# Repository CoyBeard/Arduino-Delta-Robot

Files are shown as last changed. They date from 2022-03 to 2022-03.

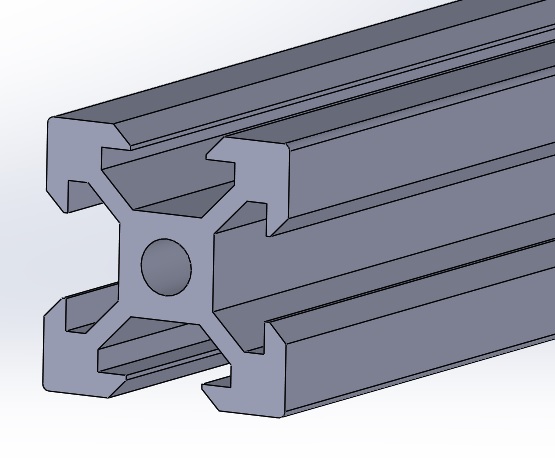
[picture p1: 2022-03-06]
2020-aluminium-profile-v-slot-solidwork2016-1.snapshot.8/2020 aluminium profile v slot.jpg

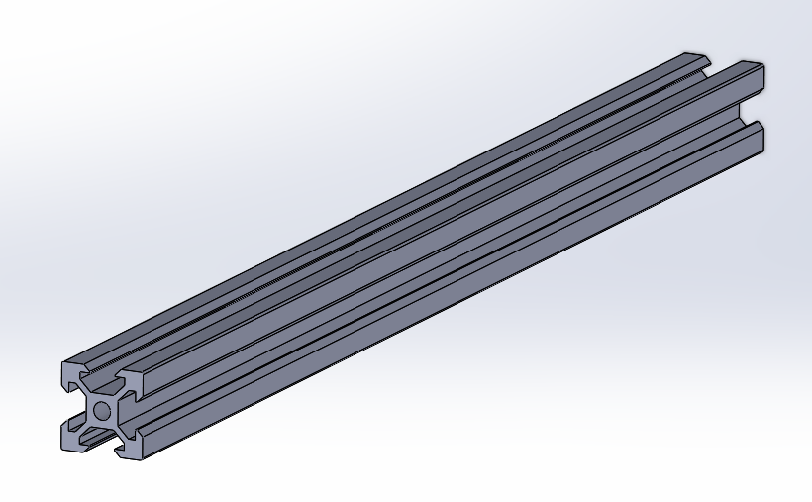
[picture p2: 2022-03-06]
2020-aluminium-profile-v-slot-solidwork2016-1.snapshot.8/2020 aluminium profile v slot solidwork 2016.png

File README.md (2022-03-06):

# Arduino-Delta-Robot
All CAD and code as seen in my YouTube video

All CAD was drawn in Autodesk Inventor But in the STEP Files the assembly is also saved as .stp

The code isn't as developed as I wanted it to be but the project had to be completed in a month

Feel free to incorporate some of these resorces into your own delta robot build!

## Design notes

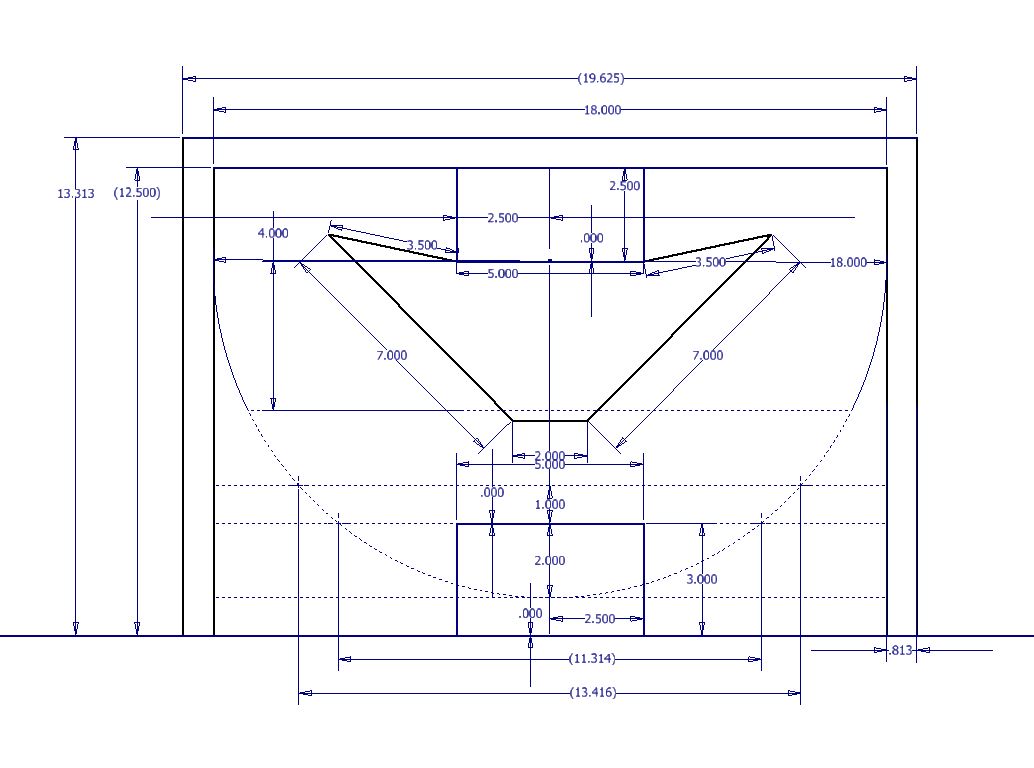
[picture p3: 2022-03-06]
Kenimatics Sketch.JPG

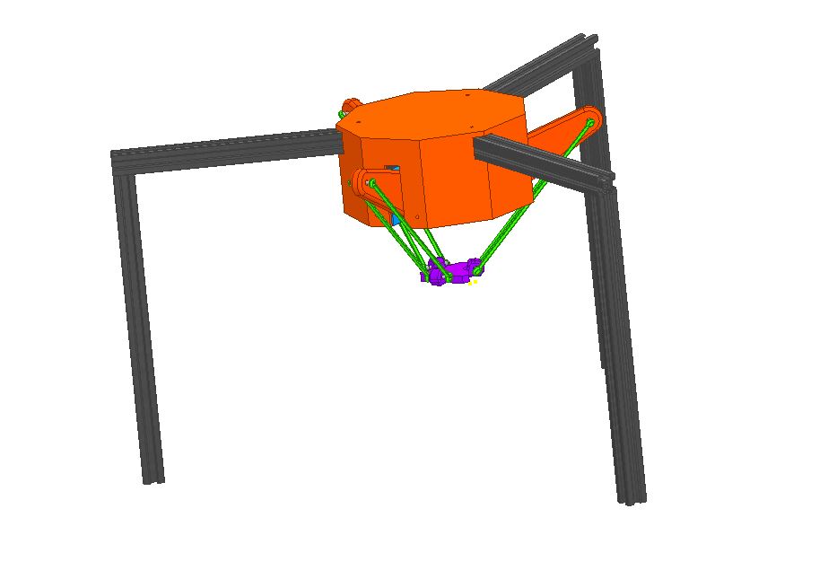
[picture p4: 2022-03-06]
Delta Robot V1 3D Model.JPG

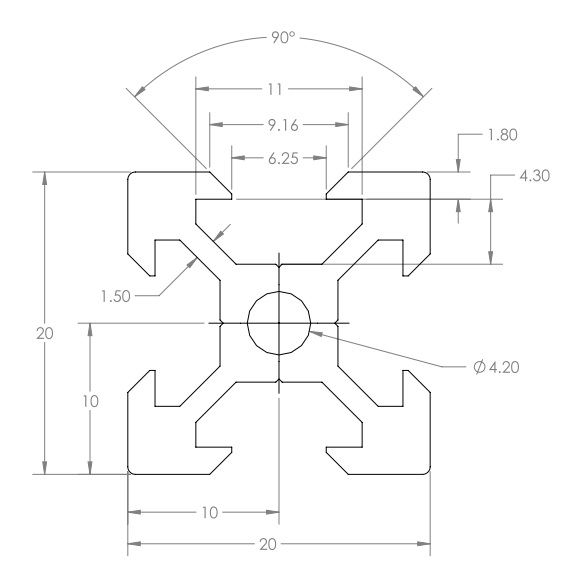
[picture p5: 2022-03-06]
2020-aluminium-profile-v-slot-solidwork2016-1.snapshot.8/5j.jpg

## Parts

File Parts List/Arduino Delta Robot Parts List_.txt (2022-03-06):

Arduino Delta Robot Parts List:
CNC 3D Printer Driver Kit, MYSWEETY 39PCS 3D Printer CNC Module Kit, 3D Printer CNC Controller Kit, Nema 17 Stepper Motor & Stepper Motor Driver with Heat Sink:

https://www.amazon.com/Printer-Driver-MYSWEETY-Controller-Stepper/dp/B08PYVPGNW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

BUD Industries JBH-4961-KO Steel NEMA 1 Sheet Metal Box 6" L x 10" W, Gray

https://www.amazon.com/gp/product/B005UPA10Y/ref=ppx_yo_dt_b_search_asin_title?ie=UTF8&psc=1

Zeelo GT2 Timing Belt Pulley, 8pcs 5mm 20 Teeth Timing Pulley Wheel and GT2 5 Meters Rubber 2mm Pitch 6mm Wide Timing Belt with Allen Wrench for 3D Printer CNC

https://www.amazon.com/gp/product/B07XG9JN5B/ref=ppx_yo_dt_b_search_asin_title?ie=UTF8&psc=1

3D Printer - Deek Robot 12Pcs/Set 3D Printer Accessories M3 Or M4 5347 Delta Buckle Ball Caps Paralleled Carbon Rod Joints - (Size: for M4)

https://www.amazon.com/gp/product/B07KX2CXX5/ref=ppx_yo_dt_b_search_asin_title?ie=UTF8&th=1

uxcell M4 x 170mm 304 Stainless Steel Fully Threaded Rod Bar Studs Fastener 10 Pcs

https://www.amazon.com/gp/product/B01MA5XUOI/ref=ppx_yo_dt_b_search_asin_title?ie=UTF8&psc=1

Iverntech 4pcs 700mm 2020 V Type Black European Standard Anodized Linear Rail Aluminum Profile Extrusion for DIY 3D Printer and CNC Machine

https://www.amazon.com/gp/product/B087PVDDX4/ref=ppx_yo_dt_b_search_asin_title?ie=UTF8&psc=1

uxcell 685ZZ Deep Groove Ball Bearings Z2 5mm X 11mm X 5mm Double Shielded Carbon Steel 12pcs

https://www.amazon.com/gp/product/B08198NQ7Y/ref=ppx_yo_dt_b_search_asin_title?ie=UTF8&psc=1

uxcell A15113000ux1262 5 Pcs 5mm x 100mm DIY RC Car Model Straight Metal Round Shaft Rod Bars (Pack of 5)

https://www.amazon.com/gp/product/B01B27MJC6/ref=ppx_yo_dt_b_search_asin_title?ie=UTF8&psc=1

VIGRUE M3 M4 M5 M6 Screw Bolt Nut Assortment Set, Button Head & Socket Head Metric Screws, 304 Stainless Steel, 588Pcs Silver

https://www.amazon.com/gp/product/B08MDXD1BN/ref=ppx_yo_dt_b_search_asin_title?ie=UTF8&psc=1

VIGRUE 184Pcs 2020 Series T Nuts, M3 M4 M5 T Slot Nut Hammer Head Fastener Nut Nickel Plated Carbon Steel with 4 Matching Wrenches for Aluminum Profile

https://www.amazon.com/gp/product/B07PLKVW69/ref=ppx_yo_dt_b_search_asin_title?ie=UTF8&psc=1

Toggle Switch Submini SPDT & DPDT On Off On Latching, Momentary, Short Shaft, Switch Assortment Kit, 31 pcs, 10 Types

https://www.amazon.com/gp/product/B08T5XS9Q3/ref=ppx_yo_dt_b_search_asin_title?ie=UTF8&psc=1
ALITOVE DC 12V 10A 120W Power Supply Adapter Transformer Switch AC 110V / 220V to DC 12V 10amp Switching Converter LED Driver for LED Strip Light CCTV Camera Security System

https://www.amazon.com/gp/product/B078RTV9C4/ref=ppx_yo_dt_b_search_asin_title?ie=UTF8&psc=1

Zixtec 10 Pack LM2596 DC-DC Buck Converter Step Down Module Power Supply DIP Output 1.25V-30V 3A (ZT001)

https://www.amazon.com/gp/product/B07VVXF7YX/ref=ppx_yo_dt_b_search_asin_title?ie=UTF8&psc=1

Liberty 22mm mounting Hole Latch Emergency Stop Button Switch red, with 60mm Emergency Stop Sign 1NO 1NC, 660V 10A (4PCS)

https://www.amazon.com/gp/product/B08ZCDHZ3R/ref=ppx_yo_dt_b_search_asin_title?ie=UTF8&psc=1

OVERTURE PLA Filament 1.75mm PLA 3D Printer Consumables, 1kg Cardboard Spool (2.2lbs), Dimensional Accuracy +/- 0.03mm, Fit Most FDM Printer (Black 1-Pack)

https://www.amazon.com/gp/product/B07PGY2JP1/ref=ppx_yo_dt_b_search_asin_title?ie=UTF8&psc=1

Eryone Silk PLA Filament 1.75mm, Silky Shiny 3D Printing Material for 3D Printer and 3D Pen, 1kg 1 Spool, 1.75mm, Silver

https://www.amazon.com/gp/product/B07KFX5THQ/ref=ppx_yo_dt_b_search_asin_title?ie=UTF8&psc=1

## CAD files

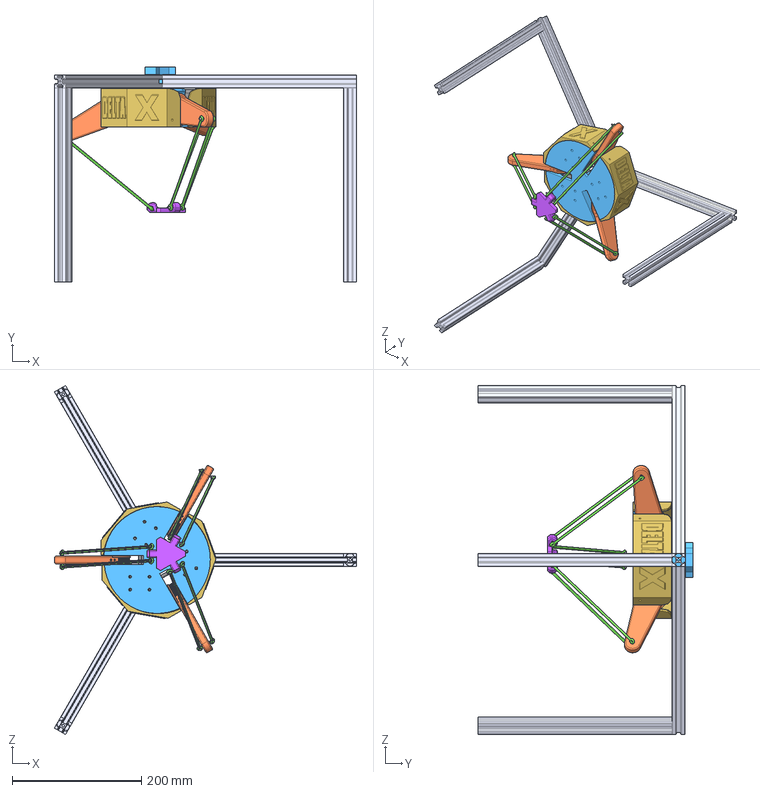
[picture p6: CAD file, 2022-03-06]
STEP Files/Delts Robot V1 Assembly.stp
467.4 x 332.5 x 539.6 mm
Delts Robot Motor Hub
Nema 17 CNC Kit Stepper Motor x 3
Delta Robot Arm Segment One x 3
Delta Robot Arm Segment Two x 6
Delts Robot Cairage
Delts Robot Arm Joint Rod x 6
2020 aluminium profile v slot solidwork2016 x 6
Small GT2 Belt Pully
Delta Robot Siding Piece x 3

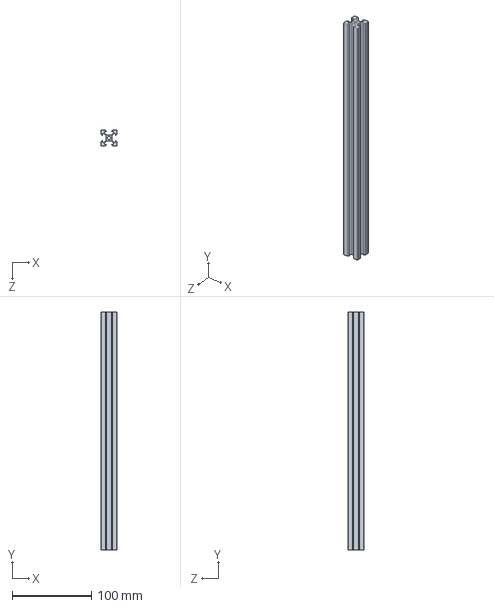
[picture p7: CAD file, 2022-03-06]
2020-aluminium-profile-v-slot-solidwork2016-1.snapshot.8/2020 aluminium profile v slot solidwork2016.SLDPRT
20.0 x 300.0 x 20.0 mm

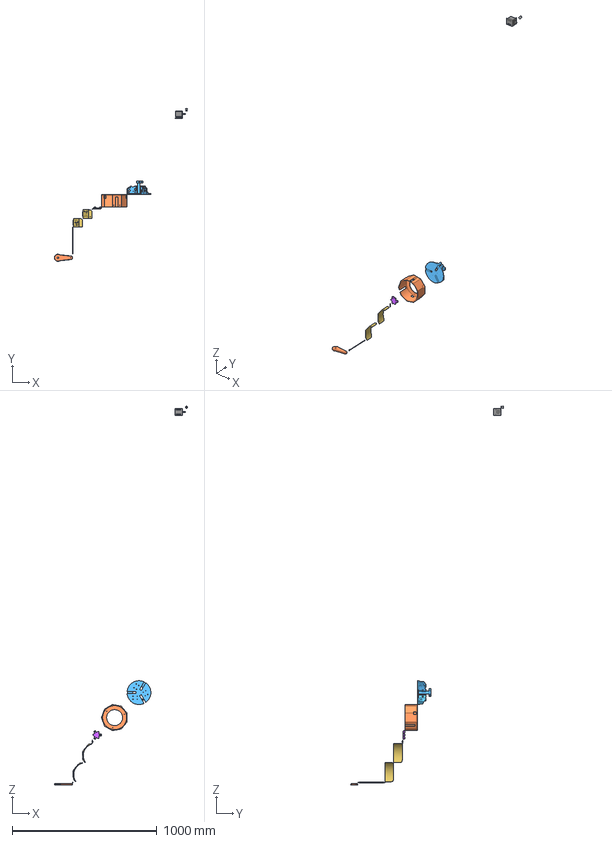
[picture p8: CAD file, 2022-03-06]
STEP Files/Other Parts.stp
921.9 x 1056.5 x 2621.0 mm
Delta Robot Arm Segment One
Delta Robot Arm Segment Two
Delta Robot Siding Piece KUKA
Delta Robot Siding Piece
Delts Robot Arm Joint Rod
Delts Robot Cairage
Delts Robot Casing
Delts Robot Motor Hub
Nema 17 CNC Kit Stepper Motor
Small GT2 Belt Pully

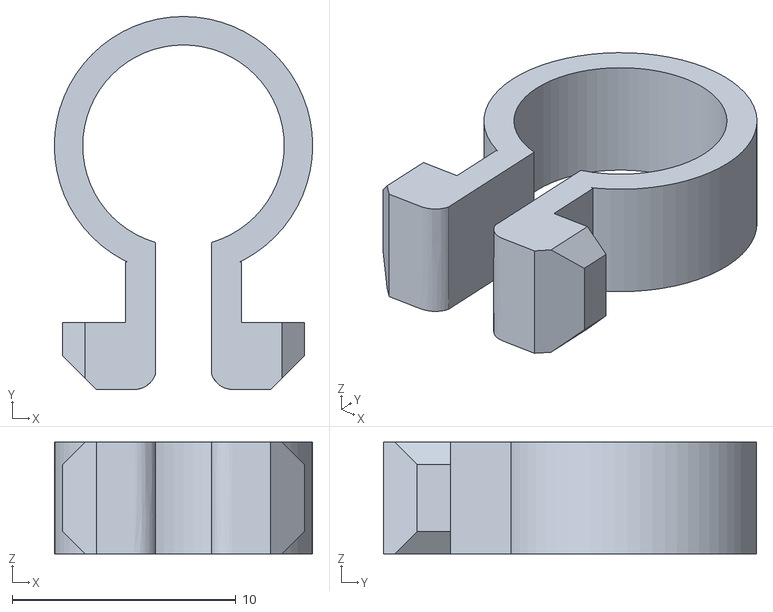
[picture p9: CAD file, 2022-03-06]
STLs V3/Cable_management_for_extrusion_2020/files/cable_2020_large (2021_05_27 07_37_48 UTC).stl
11.6 x 16.7 x 5.00

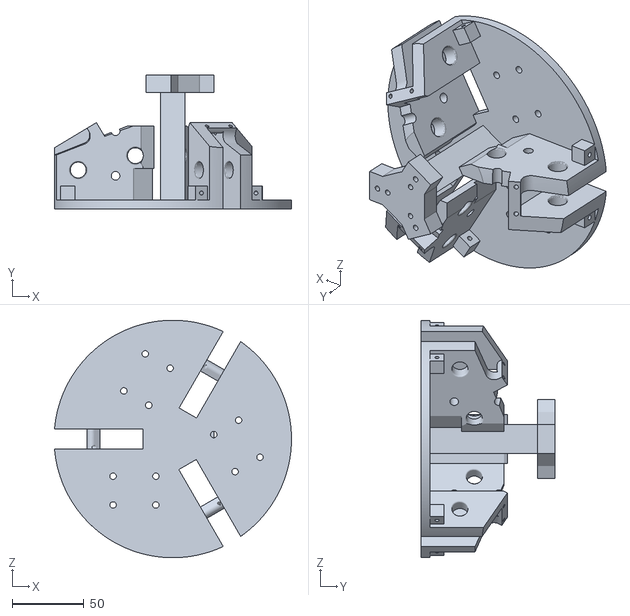
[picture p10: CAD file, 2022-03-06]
STLs V3/Delts Robot Motor Hub (2021_05_27 07_37_48 UTC).stl
164.8 x 93.0 x 165.1

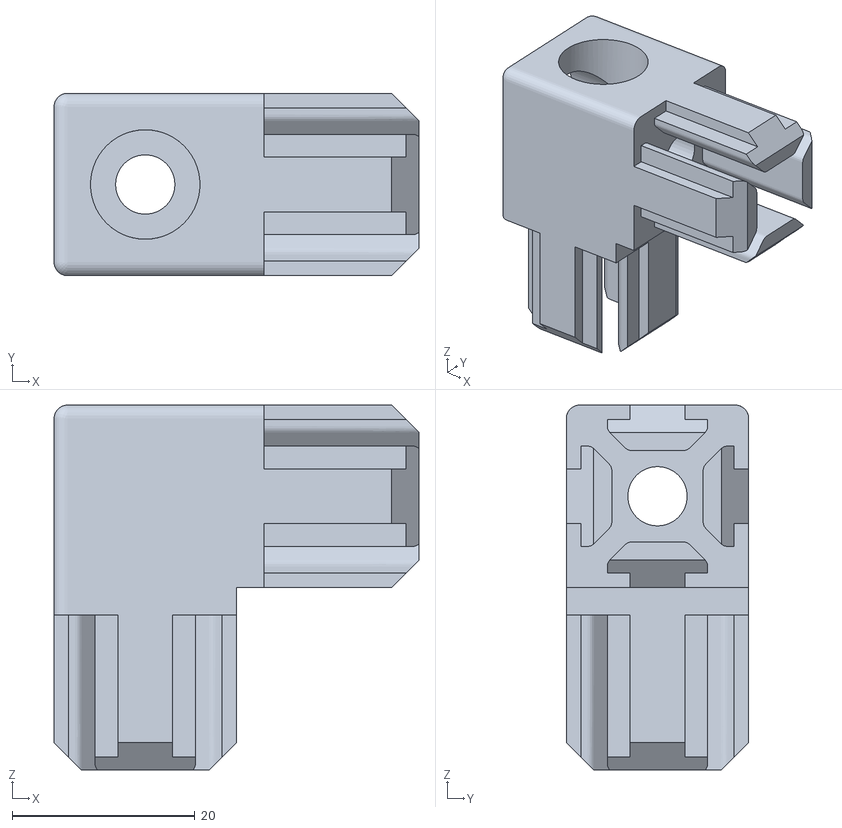
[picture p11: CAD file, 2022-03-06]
STLs V3/Legs 20x20 Corner Filler Piece/joiner internal v4 (2021_05_27 07_37_48 UTC).stl
40.0 x 20.0 x 40.0

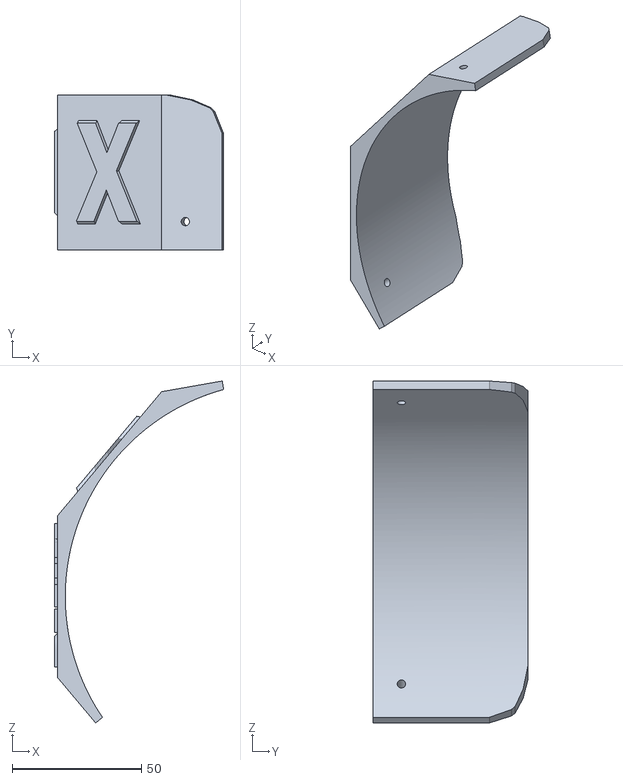
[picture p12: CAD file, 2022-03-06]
STLs V3/Delta Robot Siding Piece (2021_05_27 07_37_48 UTC).stl
65.6 x 60.0 x 132.3

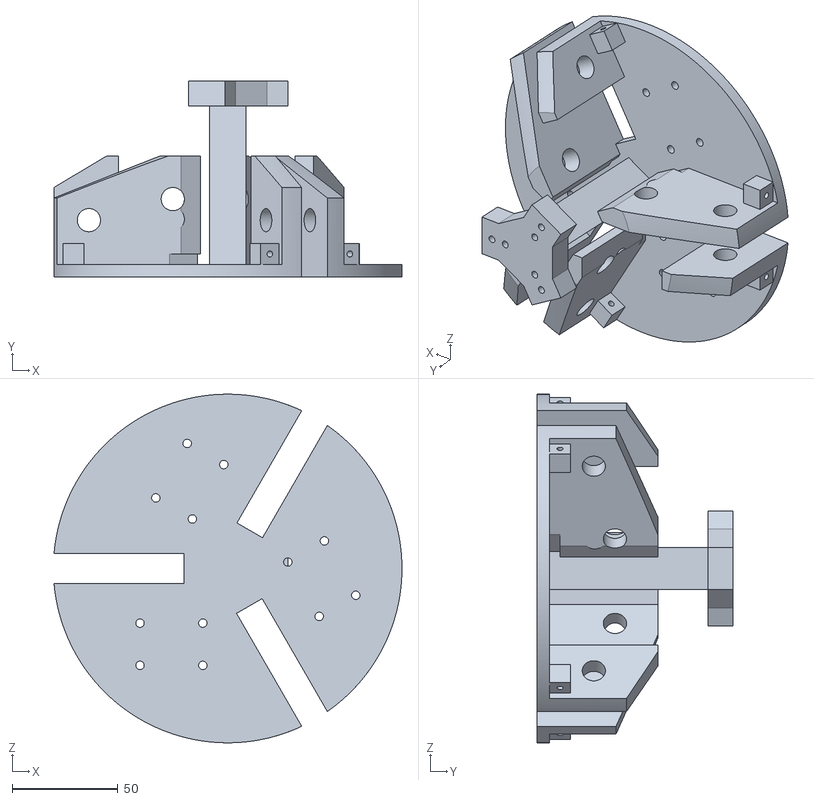
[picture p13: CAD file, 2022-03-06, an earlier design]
Stls V1/Delts Robot Motor Hub (2021_05_27 07_37_48 UTC).stl
164.8 x 93.0 x 165.1

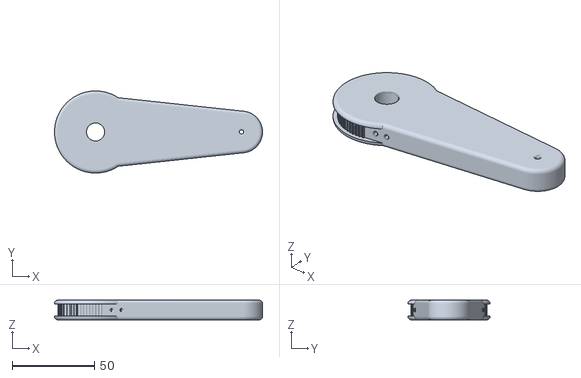
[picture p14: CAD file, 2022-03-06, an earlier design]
STLs V2/Delta Robot Arm Segment One (2021_05_27 07_37_48 UTC).stl
126.6 x 50.0 x 12.0

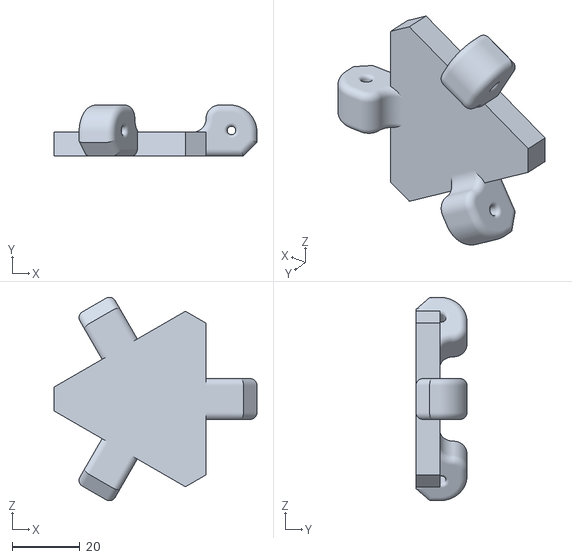
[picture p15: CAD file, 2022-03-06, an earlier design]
STLs V2/Delts Robot Cairage (2021_05_27 07_37_48 UTC).stl
59.7 x 15.0 x 59.8

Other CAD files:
Stls V1/Delta Robot Arm Segment One (2021_05_27 07_37_48 UTC).stl
2020-aluminium-profile-v-slot-solidwork2016-1.snapshot.8/2020 aluminium profile v slot solidwork2016.ipt
Delta Robot Arm Segment One.ipt
Delta Robot Arm Segment Two.ipt
Delta Robot Siding Piece KUKA.ipt
Delta Robot Siding Piece.ipt
Delts Robot Arm Joint Rod.ipt
Delts Robot Cairage.ipt
Delts Robot Casing.ipt
Delts Robot Motor Hub.ipt
Delts Robot V1 Assembly.iam
Design Sketch Top.ipt
Kenamatics and Design Sketch.ipt
Nema 17 CNC Kit Stepper Motor.ipt
OldVersions/Delta Robot Arm Segment One.0004 (2021_05_27 07_37_48 UTC).ipt
OldVersions/Delta Robot Arm Segment Two.0001 (2021_05_27 07_37_48 UTC).ipt
OldVersions/Delta Robot Mirrord Siding Piece.0001 (2021_05_27 07_37_48 UTC).ipt
OldVersions/Delta Robot Siding Piece KUKA.0002 (2021_05_27 07_37_48 UTC).ipt
OldVersions/Delta Robot Siding Piece.0002 (2021_05_27 07_37_48 UTC).ipt
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

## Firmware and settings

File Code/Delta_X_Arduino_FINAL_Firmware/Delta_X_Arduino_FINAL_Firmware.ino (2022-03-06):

#include <Servo.h>
#include <AccelStepper.h>
#include <MultiStepper.h>


//program Selection:
int RunKinematicDemmo = false;
int RunPicAndPlaceDemmo = false;
int RunProgram1 = true;
int RunProgram2 = false;
int RunProgram3 = false;


// defines pins numbers
const int stepX = 2;
const int dirX  = 5;

const int stepY = 3;
const int dirY  = 6;

const int stepZ = 4;
const int dirZ  = 7;

const int enPin = 8;

const int SOneLimit = 9;
const int STwoLimit = 10;
const int SThreeLimit = 11;

int SOneLimitState = 0;
int STwoLimitState = 0;
int SThreeLimitState = 0;

int SOneLimitReached = false;
int STwoLimitReached = false;
int SThreeLimitReached = false;

int RobotHomed = false;
int S1Homed = false;
int S2Homed = false;
int S3Homed = false;

double S1Position = 0;
double S2Position = 0;
double S3Position = 0;

double S1PreviousPosition = 0;
double S2PreviousPosition = 0;
double S3PreviousPosition = 0;

//Kinamatics

//unchanging 
double S1xSub1 = -2.759;
double S1ySub1 = 0;
double S1zSub1 = -1.063;

double S2xSub1 = 1.38;
double S2ySub1 = 2.389;
double S2zSub1 = -1.063;

double S3xSub1 = 1.38;
double S3ySub1 = -2.389;
double S3zSub1 = -1.063;

double ArmSegmentOneLength = 3.5; //in
double ArmSegmentTwoLength = 7; //in
double J1XOfset = -2.759; //in 
double J1ZOfset = 1.063; //in
double CairageXOfset = 0.962; //in
double CairageZOfset = 0.295; //in
double CairageM2XOfset = 0.481; //in
double CairageM3XOfset = -0.481; //in
double CairageM2YOfset = 0.833; //in
double CairageM3YOfset = -0.833; //in
double M2XOfset = 1.38; //in
double M3XOfset = 1.38; //in
double M2YOfset = 2.389; //in
double M3YOfset = -2.389; //in
double pi = atan(1)*4;


//changed
double S1ImaginaryDistance = 0;
double S2ImaginaryDistance = 0;
double S3ImaginaryDistance = 0;

double S1SideLengthA = 0;
double S2SideLengthA = 0;
double S3SideLengthA = 0;

double S1SideLengthB = 0;
double S2SideLengthB = 0;
double S3SideLengthB = 0;

double S1JLength = 0;
double S2JLength = 0;
double S3JLength = 0;

double S2N = 0;
double S3N = 0;

double S2P = 0;
double S3P = 0;

double S1AngleA = 0;
double S2AngleA = 0;
double S3AngleA = 0;

double S1AngleC = 0;
double S2AngleC = 0;
double S3AngleC = 0;

double S1Angle = 0;
double S2Angle = 0;
double S3Angle = 0;

double S2X2N = 0;
double S2Y2N = 0;
double S3X2N = 0;
double S3Y2N = 0;

double S2X2P = 0;
double S2Y2P = 0;
double S3X2P = 0;
double S3Y2P = 0;

double M2PLO = 3.902; //Parallel Line Ofset
double M3PLO = 3.902; //Parallel Line Ofset

double S1xSub2 = 0;
double S1ySub2 = 0;
double S1zSub2 = 0;

double S2xSub2 = 0;
double S2ySub2 = 0;
double S2zSub2 = 0;

double S3xSub2 = 0;
double S3ySub2 = 0;
double S3zSub2 = 0;

// Define some steppers and the pins the will use
AccelStepper stepper1(AccelStepper::DRIVER, 2, 5); // Defaults to AccelStepper::FULL4WIRE (4 pins) on 2, 3, 4, 5

AccelStepper stepper2(AccelStepper::DRIVER, 3, 6); // Defaults to AccelStepper::FULL4WIRE (4 pins) on 2, 3, 4, 5

AccelStepper stepper3(AccelStepper::DRIVER, 4, 7); // Defaults to AccelStepper::FULL4WIRE (4 pins) on 2, 3, 4, 5

Servo Gripper;

Servo Wrist;

const byte enablePin = 8;  // ***** pin 8 is the enable pin

//testing 

int RobotTestPhase = 0;

void setup() {
  // Sets the pins
  pinMode(enablePin, OUTPUT); // **** set the enable pin to output
  digitalWrite(enablePin, LOW); // *** set the enable pin low

  pinMode(stepX,OUTPUT);
  pinMode(dirX,OUTPUT);

  pinMode(stepY,OUTPUT);
  pinMode(dirY,OUTPUT);

  pinMode(stepZ,OUTPUT);
  pinMode(dirZ,OUTPUT);

  Gripper.attach(12);
  Wrist.attach(13);

  pinMode(SOneLimit,INPUT);
  pinMode(STwoLimit,INPUT);
  pinMode(SThreeLimit,INPUT);

  pinMode(enPin,OUTPUT);
  
  digitalWrite(enPin,LOW);

  digitalWrite(dirX,HIGH);

  digitalWrite(dirY,LOW);

  digitalWrite(dirZ,HIGH);

  stepper1.setMaxSpeed(10000000.0);
  stepper1.setAcceleration(10000.0);
    
  stepper2.setMaxSpeed(10000000.0);
  stepper2.setAcceleration(10000.0);
  
  stepper3.setMaxSpeed(10000000.0);
  stepper3.setAcceleration(10000.0);

  //Setup terminal
  Serial.begin(9600);
}

/**NOTES 
 * 
 * 
 * 
 * 1,600 steps per revolution 
 * 
 * (350 / 79) Pully ME
 * 
 * (40 / 9) Microstepping Compensation 
 * 
 * 1 real degree = (14000 / 711) input degrees about 19.5
 * 
 * **/

void CalcMotorAngles (double x, double y, double z) {

  //Motor 1
  //Cairrage offsets
  S1xSub2 = x - 0.962;
  S1ySub2 = y + 0;
  S1zSub2 = z - 0.295;
  
  //A
  S1SideLengthA = sqrt((sq(S1xSub2 - S1xSub1) + sq(S1ySub2 - S1ySub1) + sq(S1zSub1 - S1zSub1)));

  //Debugging
  Serial.print("S1SideLengthA:  ");
  Serial.print(S1SideLengthA);
  Serial.print("\n");
  
  //B
  S1SideLengthB = sqrt((sq(S1xSub2 - S1xSub2) + sq(S1ySub2 - S1ySub1) + sq(S1zSub2 - S1zSub1)));

  //Debugging
  Serial.print("S1SideLengthB:  ");
  Serial.print(S1SideLengthB);
  Serial.print("\n");
  
  //I
  S1ImaginaryDistance = sqrt((sq(S1SideLengthA) + sq(S1SideLengthB)));

  //Debugging
  Serial.print("S1ImaginaryDistance:  ");
  Serial.print(S1ImaginaryDistance);
  Serial.print("\n");

  //C
  S1AngleC = (acos(((sq(S1SideLengthA) + sq(S1ImaginaryDistance) - sq(S1SideLengthB)) / (2 * S1SideLengthA * S1ImaginaryDistance)))) * (180 / pi); 

  //Debugging
  Serial.print("S1AngleC:  ");
  Serial.print(S1AngleC);
  Serial.print("\n");

  //A
  S1AngleA = (acos(((sq(ArmSegmentOneLength) + sq(S1ImaginaryDistance) - sq(ArmSegmentTwoLength)) / (2 * ArmSegmentOneLength * S1ImaginaryDistance)))) * (180 / pi);

  //Debugging
  Serial.print("S1AngleA:  ");
  Serial.print(S1AngleA);
  Serial.print("\n");

  //Final Motor Angle
  S1Angle = ((S1AngleA + S1AngleC + 90 + 36.79) - 360) * -1;

  //Debugging
  Serial.print("S1 Final Motor Angle:  ");
  Serial.print(S1Angle);
  Serial.print("\n");


  //Motor 2   
  //Cairrage offsets
  S2xSub2 = x + 0.481;
  S2ySub2 = y + 0.833;
  S2zSub2 = z - 0.295;
   
  //A
  S2SideLengthA = sqrt((sq(S2xSub2 - S2xSub1) + sq(S2ySub2 - S2ySub1) + sq(S2zSub1 - S2zSub1)));

  //Debugging
  Serial.print("S2SideLengthA:  ");
  Serial.print(S2SideLengthA);
  Serial.print("\n");
  
  //B
  S2SideLengthB = sqrt((sq(S2xSub2 - S2xSub2) + sq(S2ySub2 - S2ySub1) + sq(S2zSub2 - S2zSub1)));

  //Debugging
  Serial.print("S2SideLengthB:  ");
  Serial.print(S2SideLengthB);
  Serial.print("\n");
  
  //I
  S2ImaginaryDistance = sqrt((sq(S2SideLengthA) + sq(S2SideLengthB)));

  //Debugging
  Serial.print("S2ImaginaryDistance:  ");
  Serial.print(S2ImaginaryDistance);
  Serial.print("\n");

  //C
  S2AngleC = (acos(((sq(S2SideLengthA) + sq(S2ImaginaryDistance) - sq(S2SideLengthB)) / (2 * S2SideLengthA * S2ImaginaryDistance)))) * (180 / pi);

  //Debugging
  Serial.print("S2AngleC:  ");
  Serial.print(S2AngleC);
  Serial.print("\n");

  //A
  S2AngleA = (acos(((sq(ArmSegmentOneLength) + sq(S2ImaginaryDistance) - sq(ArmSegmentTwoLength)) / (2 * ArmSegmentOneLength * S2ImaginaryDistance)))) * (180 / pi);

  //Debugging
  Serial.print("S2AngleA:  ");
  Serial.print(S2AngleA);
  Serial.print("\n");

  //Final Motor Angle
  S2Angle = ((S2AngleA + S2AngleC + 90 + 36.79) - 360) * -1;

  //Debugging
  Serial.print("S2 Final Motor Angle:  ");
  Serial.print(S2Angle);
  Serial.print("\n");


  //Motor 3    
  //Cairrage offsets
  S3xSub2 = x + 0.481;
  S3ySub2 = y - 0.833;
  S3zSub2 = z - 0.295;
              
  //A
  S3SideLengthA = sqrt((sq(S3xSub2 - S3xSub1) + sq(S3ySub2 - S3ySub1) + sq(S3zSub1 - S3zSub1)));

  //Debugging
  Serial.print("S3SideLengthA:  ");
  Serial.print(S3SideLengthA);
  Serial.print("\n");
  
  //B
  S3SideLengthB = sqrt((sq(S3xSub2 - S3xSub2) + sq(S3ySub2 - S3ySub1) + sq(S3zSub2 - S3zSub1)));

  //Debugging
  Serial.print("S3SideLengthB:  ");
  Serial.print(S3SideLengthB);
  Serial.print("\n");
  
  //I
  S3ImaginaryDistance = sqrt((sq(S3SideLengthA) + sq(S3SideLengthB)));

  //Debugging
  Serial.print("S3ImaginaryDistance:  ");
  Serial.print(S3ImaginaryDistance);
  Serial.print("\n");

  //C
  S3AngleC = (acos(((sq(S3SideLengthA) + sq(S3ImaginaryDistance) - sq(S3SideLengthB)) / (2 * S3SideLengthA * S3ImaginaryDistance)))) * (180 / pi);

  //Debugging
  Serial.print("S3AngleC:  ");
  Serial.print(S3AngleC);
  Serial.print("\n");

  //A
  S3AngleA = (acos(((sq(ArmSegmentOneLength) + sq(S3ImaginaryDistance) - sq(ArmSegmentTwoLength)) / (2 * ArmSegmentOneLength * S3ImaginaryDistance)))) * (180 / pi);

  //Debugging
  Serial.print("S3AngleA:  ");
  Serial.print(S3AngleA);
  Serial.print("\n");

  //Final Motor Angle
  S3Angle = ((S3AngleA + S3AngleC + 90 + 36.79) - 360) * -1;

  //Debugging
  Serial.print("S3 Final Motor Angle:  ");
  Serial.print(S3Angle);
  Serial.print("\n");
}

void StepperOneMove (int Degrees, int Direction, int SSpeed) {
  //convert steps to degrees 
  Degrees = Degrees * (14000 / 711);
  
  //Sets Direction
  if (Direction == 0) {
    digitalWrite(dirX,LOW);
  }else if (Direction == 1) {
    digitalWrite(dirX,HIGH);
  }

  //Enables the motor to move in a particular direction
  //Makes 200 pulses for making one full cycle rotation
  
  for(int x = 0; x < Degrees; x++) {
    digitalWrite(stepX,HIGH);

    delayMicroseconds(pow(1.06,((SSpeed * -1) + 139.5)));//800 home speed, 10 == 100%, 100 = 50%, 3000 = 1%

    digitalWrite(stepX,LOW);

    delayMicroseconds(pow(1.06,((SSpeed * -1) + 139.5)));//1000

    if (x >= Degrees - 1) {
      if (S1Homed == true) {
        Serial.print("S1 HOMED");
        Serial.print("\n");
        if (Direction == 0) {
          Degrees = (Degrees/(14000 / 711)) * -1;
        } else if (Direction == 1) {
          Degrees = (Degrees/(14000 / 711));
        }
        
        S1Position += Degrees;

        //Debugging
        Serial.print("S1Position:  ");
        Serial.print(S1Position);
        Serial.print("\n");
      }
    }
  }
}

void StepperTwoMove (int Degrees, int Direction, int SSpeed) {
  //convert steps to degrees 
  Degrees = Degrees * (14000 / 711);
  
  //Sets Direction
  if (Direction == 0) {
    digitalWrite(dirY,LOW);
  }else if (Direction == 1) {
    digitalWrite(dirY,HIGH);
  }

  //Enables the motor to move in a particular direction
  //Makes 200 pulses for making one full cycle rotation
  
  for(int x = 0; x < Degrees; x++) {
    digitalWrite(stepY,HIGH);

    delayMicroseconds(pow(1.06,((SSpeed * -1) + 139.5)));//800 home speed, 10 == 100%, 100 = 50%, 3000 = 1%

    digitalWrite(stepY,LOW);

    delayMicroseconds(pow(1.06,((SSpeed * -1) + 139.5)));//1000

    if (x >= Degrees - 1) {
      if (S2Homed == true) {
        Serial.print("S2 HOMED");
        Serial.print("\n");
        if (Direction == 0) {
          Degrees = (Degrees/(14000 / 711)) * -1;
        } else if (Direction == 1) {
          Degrees = (Degrees/(14000 / 711));
        }
        
        S2Position += Degrees;

        //Debugging
        Serial.print("S2Position:  ");
        Serial.print(S2Position);
        Serial.print("\n");
      }
    }
  }
}

void StepperThreeMove (int Degrees, int Direction, int SSpeed) {
  //convert steps to degrees 
  Degrees = Degrees * (14000 / 711);
  
  //Sets Direction
  if (Direction == 0) {
    digitalWrite(dirZ,LOW);
  }else if (Direction == 1) {
    digitalWrite(dirZ,HIGH);
  }

  //Enables the motor to move in a particular direction
  //Makes 200 pulses for making one full cycle rotation
  
  for(int x = 0; x < Degrees; x++) {
    digitalWrite(stepZ,HIGH);

    delayMicroseconds(pow(1.06,((SSpeed * -1) + 139.5)));//800 home speed, 10 == 100%, 100 = 50%, 3000 = 1%

    digitalWrite(stepZ,LOW);

    delayMicroseconds(pow(1.06,((SSpeed * -1) + 139.5)));//1000

    if (x >= Degrees - 1) {
      if (S3Homed == true) {
        Serial.print("S3 HOMED");
        Serial.print("\n");
        if (Direction == 0) {
          Degrees = (Degrees/(14000 / 711)) * -1;
        } else if (Direction == 1) {
          Degrees = (Degrees/(14000 / 711));
        }
        
        S3Position += Degrees;

        //Debugging
        Serial.print("S3Position:  ");
        Serial.print(S3Position);
        Serial.print("\n");
      }
    }
  }
}

void Home () {
  //read S1 limit switch 
  SOneLimitState = digitalRead(SOneLimit);

  //find M1 limit 
  if (SOneLimitState == HIGH && SOneLimitReached == false && STwoLimitReached == false && SThreeLimitReached == false) {
    //move 1 degree at a time 
    StepperOneMove(1, 0, 30);
  }else if (SOneLimitState == LOW) {
    //S1 Homed 
    S1Homed = true;
    S1Position = 0;
    stepper1.setCurrentPosition (0);
    stepper1.moveTo(45 * (14000 / 711));
    while (stepper1.distanceToGo() > 0) {
      stepper1.run();
    }
    
    //toggle var
    if (stepper1.distanceToGo() <= 0) {
      SOneLimitReached = true;
      Serial.print("S1 HOMED");
      Serial.print("\n");
      
      delay(300);
    }
  }
  
  //read S1 limit switch 
  STwoLimitState = digitalRead(STwoLimit);

    //find M2 limit 
  if (STwoLimitState == HIGH && SOneLimitReached == true && STwoLimitReached == false && SThreeLimitReached == false) {
    //move 1 degree at a time 
    StepperTwoMove(1, 0, 30);
  }else if (STwoLimitState == LOW) {
    //S1 Homed 
    S2Homed = true;
    S2Position = 0;
    stepper2.setCurrentPosition (0);
    stepper2.moveTo(45 * (14000 / 711));
    while (stepper2.distanceToGo() > 0) {
      stepper2.run();
    }
    
    //toggle var
    if (stepper2.distanceToGo() <= 0) {
      STwoLimitReached = true;
      Serial.print("S2 HOMED");
      Serial.print("\n");
      
      delay(300);
    }
  }

  //read S1 limit switch 
  SThreeLimitState = digitalRead(SThreeLimit);

    //find M3 limit 
  if (SThreeLimitState == HIGH && SOneLimitReached == true && STwoLimitReached == true && SThreeLimitReached == false) {
    //move 1 degree at a time 
    StepperThreeMove(1, 0, 30);
  }else if (SThreeLimitState == LOW) {
    //S1 Homed 
    S3Homed = true;
    S3Position = 0;
    stepper3.setCurrentPosition (0);
    stepper3.moveTo(45 * (14000 / 711));
    while (stepper3.distanceToGo() > 0) {
      stepper3.run();
    }
    
    //toggle var
    if (stepper3.distanceToGo() <= 0) {
      SThreeLimitReached = true;
      Serial.print("S3 HOMED");
      Serial.print("\n");
        
      delay(300);

      //toggle var
      SThreeLimitReached = true;
      RobotHomed = true;
      S1Homed = false;
      S2Homed = false;
      S3Homed = false;
  
      RobotTestPhase += 1;
  
      delay(2000);
    }
  }
}

void loop() {
  
  if (RobotHomed == false) {
    Home();
  }

  if (RobotHomed == true) {

    if (RunProgram1 == true) {

      Wrist.write(0);

      Gripper.write(0);

      delay(3000);
      
      Wrist.write(180);

      Gripper.write(180);

      delay(3000);
    }

    if (RunProgram2 == true) {
      
    }

    if (RunProgram3 == true) {
      
    }

    if (RunPicAndPlaceDemmo == true) {
      //Move to Point
      CalcMotorAngles(-1, 0, 3);
      stepper1.moveTo(S1Angle * (14000 / 711));
      stepper2.moveTo(S2Angle * (14000 / 711));
      stepper3.moveTo(S3Angle * (14000 / 711));
      while (stepper1.distanceToGo() !=  0 || stepper2.distanceToGo() != 0 || stepper3.distanceToGo() != 0) {
        stepper1.run();
        stepper2.run();
        stepper3.run();
      } if (stepper1.distanceToGo() == 0 && stepper2.distanceToGo() == 0 && stepper3.distanceToGo() == 0) {
        Serial.print("0, 0");
        Serial.print("\n");
        //delay(3000);
      }

      //Move to Point
      CalcMotorAngles(2, 0, 2);
      stepper1.moveTo(S1Angle * (14000 / 711));
      stepper2.moveTo(S2Angle * (14000 / 711));
      stepper3.moveTo(S3Angle * (14000 / 711));
      while (stepper1.distanceToGo() != 0 || stepper2.distanceToGo() != 0 || stepper3.distanceToGo() != 0) {
        stepper1.run();
        stepper2.run();
        stepper3.run();
      } if (stepper1.distanceToGo() == 0 && stepper2.distanceToGo() == 0 && stepper3.distanceToGo() == 0) {
        Serial.print("2, 0");
        Serial.print("\n");
        //delay(3000);
      }

      //Move to Point
      CalcMotorAngles(2, 0, 5);
      stepper1.moveTo(S1Angle * (14000 / 711));
      stepper2.moveTo(S2Angle * (14000 / 711));
      stepper3.moveTo(S3Angle * (14000 / 711));
      while (stepper1.distanceToGo() != 0 || stepper2.distanceToGo() != 0 || stepper3.distanceToGo() != 0) {
        stepper1.run();
        stepper2.run();
        stepper3.run();
      } if (stepper1.distanceToGo() == 0 && stepper2.distanceToGo() == 0 && stepper3.distanceToGo() == 0) {
        Serial.print("0, 0");
        Serial.print("\n");
        //delay(3000);
      }

      //Move to Point
      CalcMotorAngles(2, 0, 2);
      stepper1.moveTo(S1Angle * (14000 / 711));
      stepper2.moveTo(S2Angle * (14000 / 711));
      stepper3.moveTo(S3Angle * (14000 / 711));
      while (stepper1.distanceToGo() != 0 || stepper2.distanceToGo() != 0 || stepper3.distanceToGo() != 0) {
        stepper1.run();
        stepper2.run();
        stepper3.run();
      } if (stepper1.distanceToGo() == 0 && stepper2.distanceToGo() == 0 && stepper3.distanceToGo() == 0) {
        Serial.print("2, 0");
        Serial.print("\n");
        //delay(3000);
      }

      //Move to Point
      CalcMotorAngles(-1, 0, 3);
      stepper1.moveTo(S1Angle * (14000 / 711));
      stepper2.moveTo(S2Angle * (14000 / 711));
      stepper3.moveTo(S3Angle * (14000 / 711));
      while (stepper1.distanceToGo() !=  0 || stepper2.distanceToGo() != 0 || stepper3.distanceToGo() != 0) {
        stepper1.run();
        stepper2.run();
        stepper3.run();
      } if (stepper1.distanceToGo() == 0 && stepper2.distanceToGo() == 0 && stepper3.distanceToGo() == 0) {
        Serial.print("0, 0");
        Serial.print("\n");
        //delay(3000);
      }

      //Move to Point
      CalcMotorAngles(-1, 0, 5);
      stepper1.moveTo(S1Angle * (14000 / 711));
      stepper2.moveTo(S2Angle * (14000 / 711));
      stepper3.moveTo(S3Angle * (14000 / 711));
      while (stepper1.distanceToGo() !=  0 || stepper2.distanceToGo() != 0 || stepper3.distanceToGo() != 0) {
        stepper1.run();
        stepper2.run();
        stepper3.run();
      } if (stepper1.distanceToGo() == 0 && stepper2.distanceToGo() == 0 && stepper3.distanceToGo() == 0) {
        Serial.print("0, 0");
        Serial.print("\n");
        //delay(3000);
      }
      
    }
    
    if (RunKinematicDemmo == true) {
      //Move to Point
      CalcMotorAngles(0, 0, 4);
      stepper1.moveTo(S1Angle * (14000 / 711));
      stepper2.moveTo(S2Angle * (14000 / 711));
      stepper3.moveTo(S3Angle * (14000 / 711));
      while (stepper1.distanceToGo() != 0 || stepper2.distanceToGo() != 0 || stepper3.distanceToGo() != 0) {
        stepper1.run();
        stepper2.run();
        stepper3.run();
      } if (stepper1.distanceToGo() == 0 && stepper2.distanceToGo() == 0 && stepper3.distanceToGo() == 0) {
        Serial.print("0, 0");
        Serial.print("\n");
        //delay(3000);
      }

      //Move to Point
      CalcMotorAngles(0, 0, 6);
      stepper1.moveTo(S1Angle * (14000 / 711));
      stepper2.moveTo(S2Angle * (14000 / 711));
      stepper3.moveTo(S3Angle * (14000 / 711));
      while (stepper1.distanceToGo() != 0 || stepper2.distanceToGo() != 0 || stepper3.distanceToGo() != 0) {
        stepper1.run();
        stepper2.run();
        stepper3.run();
      } if (stepper1.distanceToGo() == 0 && stepper2.distanceToGo() == 0 && stepper3.distanceToGo() == 0) {
        Serial.print("0, 0");
        Serial.print("\n");
        //delay(3000);
      }
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
